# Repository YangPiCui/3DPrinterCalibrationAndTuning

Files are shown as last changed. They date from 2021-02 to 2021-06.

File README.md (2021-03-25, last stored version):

# 3DPrinterCalibrationAndTuning
Instruction is based on the Cura Slicer and Doogell Vega.  
     
a temporary value = 0.1;  //comments  
> Filament Diameter = 1.75mm; // a permanent value 

## 0. Calibrate Printer and Fix Independent Slicer Parameters
### Levelling
0. Set the hotend and the bed are at their printing temperatures. 
1. Level the print bed against the print head.
2. Level the printer with a bubble leveler on the print bed.

### 0.0 Acquire Printer Basic Parameters
X/Y uncertainty = 0.1mm;  
Z resolution = 0.04mm;    
> Max hotend temperature = 260;  
> Max bed temperature = 70;  

> X direction = ↓; X range = 0-250;  
> Y direction = →, Y range = 0-293; //Belt starts to slip at 294  
> Z direction = up, Z range = 0-175; //with glass bed. Default 300.
> Rectangular; Heated bed; G-code flavor = RepRap;  
  
Printhead ([how these values are defined](https://community.ultimaker.com/topic/18484-printhead-settings/))  
> X min = -29; //measured in the negative x direction  
> Y min = -37; //measured in the negative y direction  
> X max = 60; //measured in the positive x direction  
> Y max = 37; //measured in the positive y direction  
> Gantry Height = 82mm; //the lowest point on the rails in which the extruder assembly rides to the print bed when the nozzle is at height Z=0  
  
Extruder 0:   
> Compatible material diameter = 1.75 mm;  
> Nozzle size = 0.6mm; //default 0.4mm  
> Nozzle Flat = 1.2mm.  
    
### 0.1 Calibrate Printer XYZ Steps/mm ([reference](https://www.youtube.com/watch?v=W4CsD5lRvHY&feature=emb_logo))  
During this step, make sure the hotend is not obstructed in any direction!  

Default steps/mm X&Y = 80; Z = 400;  

X axis  
[Y = 0, Z = 3]; intended travel = 250mm; actual = 250.2mm;  
[Y = 150, Z = 3]; intended travel = 250mm; actual = 250.4mm; <- Scale Model by .99840  
[Y = 300, Z = 3]; intended travel = 250mm; actual = 250.4mm;  
  
Y axis  
[X = 0, Z = 3]; intended travel = 300mm; actual = 297.5mm;  
[X = 125, Z = 3]; intended travel = 300mm; actual = 299mm; <- Scale Model by 1.00334  
[X = 250, Z = 3]; intended travel = 300mm; actual = 298mm;  
  
Z axis  
[X = 0, Y = 0]; intended travel = 297mm; actual = 296.2mm;  
[X = 0, Y = 300]; intended travel = 297mm; actual = 296.5mm ;  
[X = 125, Y = 150]; intended travel = 297mm; actual = 297mm; <- Average of all measurements  
[X = 250, Y = 0]; intended travel = 297mm; actual = 296.2mm;  
[X = 250, Y = 300]; intended travel = 297mm; actual = 296.25mm;  

existing value * desired value / actual value = corrected value  
> X = 80 * .99840 = 79.872;  
> Y = 80 * 1.00334 = 80.267;  
> Z = 400 * 1.0019 = 400.76;  
  
### 0.2 Calibrate Printer Extruder Steps/mm (E) ([reference](https://mattshub.com/blog/2017/04/19/extruder-calibration))  
Remove the hot end.  
Calibrate when filament changes.  
Default steps/mm E = 95.8 (extrusion multiplier);  
corrected value = existing value * desired value / actual value
> E steps/mm = 96.67 * 200 / 200.5 = 96.5;  

### 0.3 Calculate Printer Max Mechanical Speed
> X/Y Max Speed = 300mm/s;  
> Z Max Speed =  12.5mm/s;   
> E Max Speed = 28 mm/s;   

### 0.4 Fix Independent Slicer Parameters 
Load default cura profile "Fine", which has a layer height of 0.1mm.  
Choose these constant parameter(s) for production print:  
> Layer height = 0.4; //A multiple of 0.04mm and should be less than 80% of nozzle diameter. [stepper motor magic number](https://www.youtube.com/watch?v=WIkT8asT90A).  [Which layer height gives you the strongest 3D prints](https://www.youtube.com/watch?v=fbSQvJJjw2Q&t=644s).  
> Line Width = 1.0; //Minimum Line Width = Nozzle Size + Layer Height;  Maximum Line Width = Nozzle Flat Size + Layer Height;  [understand line width](https://dyzedesign.com/2018/07/3d-print-speed-calculation-find-optimal-speed/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,bigger%20nozzles%20and%20layer%20height.)
> Print Speed = 50mm/s; // [Maximum 3D Printing Speed Calculator](https://dyzedesign.com/3d-printing-speed-calculator/).
> Travel Speed = 300;  
> Top/Bottom Pattern = Bottom Pattern Initial Layer = Zig Zag;  
> Infill Pattern = Gyroid;  //[increased strength for the lowest weight.](https://support.ultimaker.com/hc/en-us/articles/360012607079-Infill-settings) [Testing 3D printed infill pattern.](https://www.youtube.com/watch?v=upELI0HmzHc)
> Optimize Wall Printing Order = True;  
> Print Thin Walls = True;  
> Z Seam Alignment = Random;  

## 1. Fix Inter-dependent Slicer Parameters
### 1.0 Remove Jerk ([reference](https://all3dp.com/2/3d-printing-speed-optimal-settings/) | [reference](https://www.thingiverse.com/thing:1586548) | [Printing at 300mm/s](https://dyzedesign.com/2016/10/printing-300-mm-s-part-1-basics-hardware/) | [Motion Profile](https://www.controleng.ca/servosoft/SSHelp1033/source/MotionProfile.htm) | [reference](https://www.reddit.com/r/3Dprinting/comments/99rhah/what_is_jerk_really_measuring/))
> Print Accelaration = 250 mm/s^2;  
> Print Jerk = 0.001 mm/s; //print head's max speed at which it can change direction 

### 1.1 Optimize Cooling
> Enable Print Cooling = false; //I prefer natural cooling for better layer bonding  

### 1.2 Tune Hotend PID ([reference](https://reprap.org/wiki/PID_Tuning)) 
> The default PIDs are usually good: P = 10; I = 2.5; D = 100;  

### 1.3 Optimize Hotend Temperature [Print Some Test Objects At This Step] ([reference](https://e3d-online.dozuki.com/Guide/Calibrating+Printing+temperature/91))(https://matterhackers.dozuki.com/Guide/PID+Tuning/6)) | [reference](https://reprap.org/wiki/PID_Tuning) | [reference]([https://reprap.org/wiki/G-code#M928:_Start_SD_logging](https://reprap.org/wiki/G-code#M928:_Start_SD_logging))) 
Stack the [Smart compact temperature calibration Towers](https://www.thingiverse.com/thing:2729076)   on top of each other [in Cura](CalibrationObjects/TemperatureTower.3mf). Make sure you import the models only (without importing profiles)! Use "Extensions" -> "Post Processing" -> "ChangeAtZ" to set the temperatures.  (1.4mm, 11.4mm, 21.4mm ...)  
Infill = 15%;  
Support = No;  
Build Plate Adhesion = Skirt;  
> Printing Temperature = 210 Celsius;  
> Build Plate Temperature = 35;  //[reference](https://all3dp.com/2/the-best-pla-print-temperature-how-to-achieve-it/)  | [Correct elephant foot and print edge bending.]  

### 1.4 Minimize Stringing [Print Some Test Objects At This Step] ([reference](https://all3dp.com/2/3d-print-stringing-easy-ways-to-prevent-it/) | [reference](https://www.thingiverse.com/thing:2219103))
[StringTest.stl](CalibrationObjects/StringTest.stl)   
Wall Line Count = 3;   
Top Layers = Bottom Layers = 4;   
Infill Density = 15;  
Support = No;  
Build Plate Adhesion = skirt;  
> Retract Before Outer Wall = True;  
> Retraction Distance = 2mm;  
> Retraction Speed = 30mm/s; // same as the E Max Speed
> Combing Mode = Not in Skin;  
> Max Comb Distance With No Retract = 15mm;  
> Z Hop When Retracted = False;  
  
### 1.5 Calibrate Flow Rate [Print Some Test Objects At This Step]  ([reference](https://e3d-online.dozuki.com/Guide/Flow+rate+%28Extrusion+multiplier%29+calibration+guide./89))  
[FlowRateCalibration.3mf](CalibrationObjects/FlowRateCalibration.3mf) Make sure you import the models only (without importing profiles)!  
Wall Line Count = 2; 
Top Layers = Bottom Layers = 0;  
Infill Density = 0;  
Build Plate Adhesion Type = Brim;   
  
Corrected Flow Rate = Existing flow rate * Desired wall thickness / actual wall thickness
> Flow = 92;
(https://all3dp.com/1/common-3d-printing-problems-troubleshooting-3d-printer-issues/)  

### 1.6 Calibrate Horizontal Expansion [Print Some Test Objects At This Step] ([reference](https://www.youtube.com/watch?v=UUelLZvDelU) | [reference](https://bradshacks.com/3d-printing-tolerancing/))
[HorizontalExpansionCalibration.3mf](CalibrationObjects/HorizontalExpansionCalibration.3mf) Use "import model" instead of "import project"! 
> Connect Infill Lines;  
> Randomize Infill Start;  
Support = None;  
Build Plate Adhesion = Skirt;  
Skirt Line Count = 2;  
Skirt Distance = 5mm;  
Skirt Minimum Length = 50mm;  
> Horizontal Expansion = Initial Layer Horizontal Expansion = -0.05; //use a vernier caliber
> Hole Horizontal Expansion = 0.1; //positive value makes bigger holes

### 1.7 Optimize Initial Layer Adhesion
> Initial Layer Height = 0.4-0.1 = 0.3; // Set the initial layer height (ILH) to be the layer height (0.4mm) from the buildplate. I used a piece of paper 0.1mm thick to level the bed. ILH == multiple of Z-resolution(0.04mm) && (>= Layer Height) && (<= 80% of nozzle size) 
> Z Offset = -0.0mm; //[cura z offset simply explained](https://all3dp.com/2/cura-z-offset-simply-explained/) 
> Initial Layer Speed = 20mm/s; //[Tune First Layer.](https://www.youtube.com/watch?v=pAFDEn3wGYo)  
> Initial Layer Flow = 92*0.4/0.3 = 123; //scaled from the Flow value; = actual initial layer height / initial layer height

### 1.8 Determine Max Overhang Angle [Print Some Test Objects At This Step]
[How to calculate maximum overhang angle](https://omni3d.com/blog/how-to-calculate-maximum-overhang-angle/)   
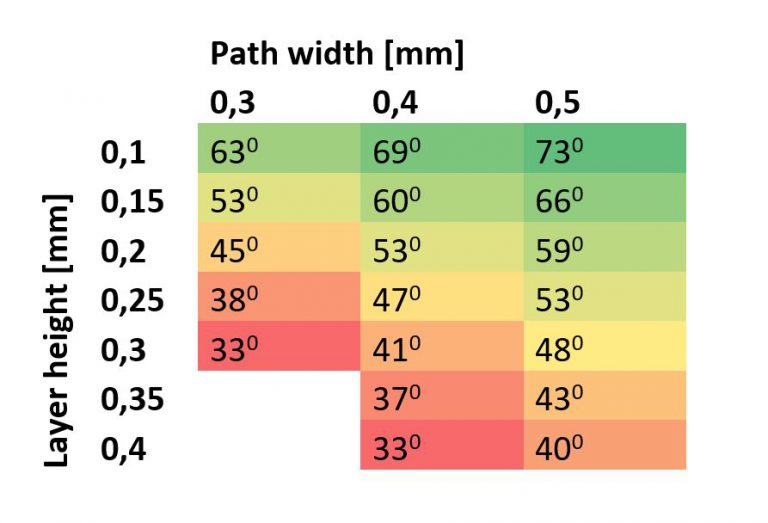
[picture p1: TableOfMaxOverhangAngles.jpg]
  
Print an overhang angle test object to confirm this.  

## 2. Miscellaneous Settings  
> Infill Travel Optimization = On;  
> Avoid Supports When Travelling = True;  
> Slicing Tolerance = Inclusive;  
   
### 2.0 Situational Settings  
> Wall Line Count = Top Layers = Bottom Layers = 6; //[3-4 layers && 15-20% for good strength. Max strength with 5-6 layers and 25-30% infill.](https://www.youtube.com/watch?v=sAZpnlzCwiU)  
> Infill = 30%;  
> Infill Pattern = Gyroid;
> Top/Bottom Pattern = Zig Zag;
> Bottom Pattern Initial Layer = Zig Zag; // Top Bottom Layer number a multiple of 2 preferred
> Build Plate Adhesion Type = Brim;  
> Brim Line Count = 1;
> Tree Support Branch Angle = 30; // This depends on the layer height and line width of the tree support walls
> Use Adaptive Layers = True; //set to false by default.
> Adaptive Layers Maximum Variation = 0.08; //half of line height  
> Adaptive Layers Variation Setp Size = 0.04;  
> Adaptive Layers Topography Size = 0.16; //same as line height

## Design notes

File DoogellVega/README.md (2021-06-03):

# Doogell Vega
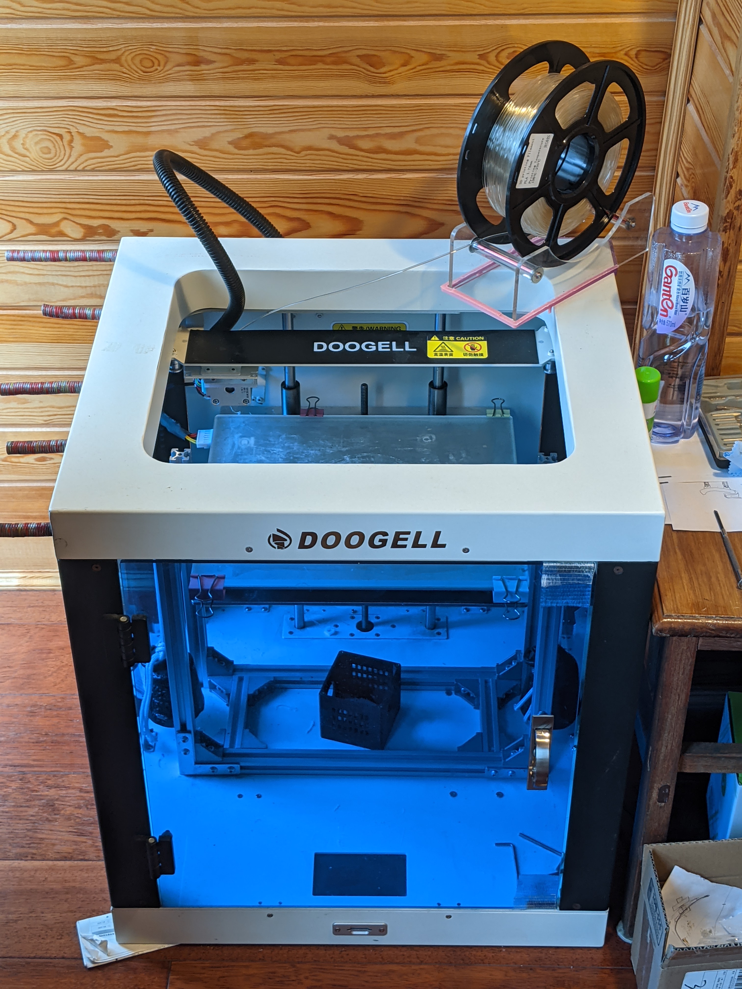
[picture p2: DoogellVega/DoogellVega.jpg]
  
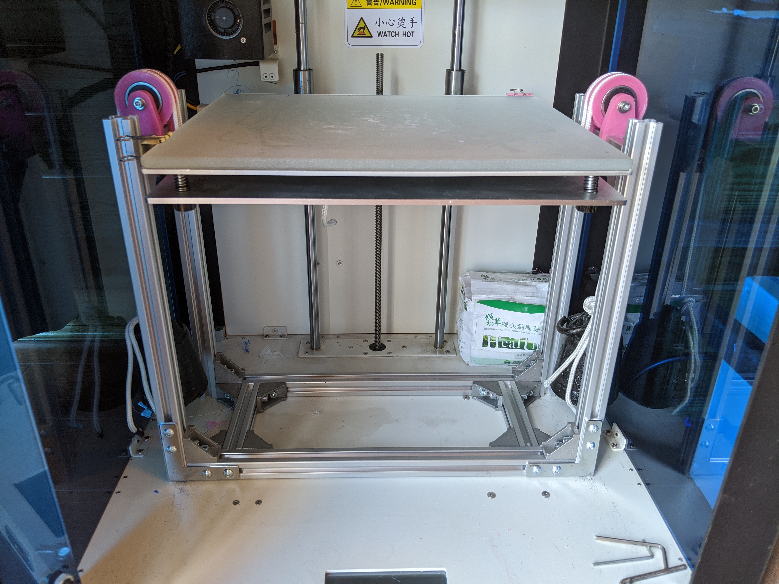
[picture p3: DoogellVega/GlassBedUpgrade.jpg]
  
Bought 2nd hand for $500; CoreXY structure; Imported stepper motors and linear rails.  
Touch screen is inaccurate to the touch; One has to use Gcode to change the default printer parameters.   
Rectangular build plate; Heated bed; Replaced bed cover with tempered sanded-surface glass.   
Added plexiglass hud.
     
Instruction is based on the Cura Slicer.  
a temporary value = 0.1;  //comments  
> Filament Diameter = 1.75mm; // a permanent value 

## 0. Calibrate Printer and Set Independent Slicer Parameters
### 0.0 Bed Levelling
0. Set the hotend and the bed at their intended printing temperatures. 
1. Level the print bed against the print head with a strip of A4 paper (usually 0.1mm thick).
2. Level the entire printer with a bubble leveler placed on the print bed.

### 0.1 Acquire Printer Specifications
> Filament Diameter = 1.75mm;  
> Rectangular; Heated bed; G-code flavor = RepRap;  
> Max hotend temperature = 260;  
> Max bed temperature = 70;  
> X direction = ↓; X range = 0-250; //Positive direction from the back to the front  
> Y direction = →, Y range = 0-240; //Belt starts to slip at 294; fan mod limits travel to 240
> Z direction = up, Z range = 0-200; //for glass bed; Default is 300.   
> X/Y resolution = 0.1mm;  
> Z resolution = 0.04mm;  
  
Printhead ([how these values are defined](https://community.ultimaker.com/topic/18484-printhead-settings/))  
> X min = -29-9; //measured in the negative x direction  
> Y min = -37-12; //measured in the negative y direction  
> X max = 60; //measured in the positive x direction  
> Y max = 37+13; //measured in the positive y direction  
> Gantry Height = 92+13mm; //the lowest point on the rails in which the extruder assembly rides to the print bed when the nozzle is at height Z=0   
  
Extruder 0:    
> Nozzle size = 0.3mm; //default 0.4mm
> Nozzle Flat = 1.2mm.  
    
### 0.2 Calibrate Printer XYZ Steps/mm ([reference](https://www.youtube.com/watch?v=W4CsD5lRvHY&feature=emb_logo))  
During this step, make sure the hotend is not obstructed in any direction!  

Default steps/mm X&Y = 80; Z = 400;  //(Machine LCD screen under "Advanced Settings")   

X axis  
[Y = 0, Z = 3]; intended travel = 250mm; actual = 250.2mm;  
[Y = 150, Z = 3]; intended travel = 250mm; actual = 250.4mm; <- Scale Model by .99840  
[Y = 300, Z = 3]; intended travel = 250mm; actual = 250.4mm;  
  
Y axis  
[X = 0, Z = 3]; intended travel = 300mm; actual = 297.5mm;  
[X = 125, Z = 3]; intended travel = 300mm; actual = 299mm; <- Scale Model by 1.00334  
[X = 250, Z = 3]; intended travel = 300mm; actual = 298mm;  
  
Z axis  
[X = 0, Y = 0]; intended travel = 297mm; actual = 296.2mm;  
[X = 0, Y = 300]; intended travel = 297mm; actual = 296.5mm ;  
[X = 125, Y = 150]; intended travel = 297mm; actual = 297mm; <- Average of all measurements  
[X = 250, Y = 0]; intended travel = 297mm; actual = 296.2mm;  
[X = 250, Y = 300]; intended travel = 297mm; actual = 296.25mm;  

existing value * desired value / actual value = corrected value  
> X = 80 * .99840 = 79.872;  
> Y = 80 * 1.00334 = 80.267;  
> Z = 400 * 1.0019 = 400.76;  
  
Apply the Gcodes in "SetXYZStepsPerMm.gcode" to save the calibrated values.  
  
### 0.3 Calibrate Printer Extruder Steps/mm (E) ([reference](https://mattshub.com/blog/2017/04/19/extruder-calibration))  
Remove the hot end.  
Calibrate when filament changes.  
Default steps/mm E = 95.8 (extrusion multiplier);  
corrected value = existing value * desired value / actual value
> E steps/mm = 96.67 * 200 / 200.5 = 96.5;  

### 0.4 Calculate Printer Max Mechanical Speed
Apply the Gcodes in "MeasureXYZMaxSpeeds.gcode" to measure the max speeds.  
> X/Y Max Speed = 300mm/s; //approximation  
> Z Max Speed =  12.5mm/s; //approximation  
> E Max Speed = 28 mm/s; //filament extrusion speed     

### 0.5 Tune PID
> Default PID works well: P = 10; I = 2.5; D = 100; (Machine LCD screen under "Advanced Settings")  
  
The printer can not display the results of PID auto tuning on its LCD screen; Neither can it log the results onto a SD card.  
Integrate TuneAndLogTemperaturePID.gcode into the printer's Start G-code in Cura to set and to save the temperature PID. 
  
### 0.6 Set Independent Slicer Parameters 
Load default cura profile "Fine", which has a layer height of 0.1mm.  
Choose these constant parameter(s) for production print:  
> Layer height = 0.4; //A multiple of 0.04mm and should be less than 80% of nozzle diameter. [stepper motor magic number](https://www.youtube.com/watch?v=WIkT8asT90A).  [Which layer height gives you the strongest 3D prints](https://www.youtube.com/watch?v=fbSQvJJjw2Q&t=644s).  
> Line Width = 1.0; //Minimum Line Width = Nozzle Size + Layer Height;  Maximum Line Width = Nozzle Flat Size + Layer Height;  [understand line width](https://dyzedesign.com/2018/07/3d-print-speed-calculation-find-optimal-speed/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,bigger%20nozzles%20and%20layer%20height.)
> Print Speed = 50mm/s; // [Maximum 3D Printing Speed Calculator](https://dyzedesign.com/3d-printing-speed-calculator/).
> Travel Speed = 300;  
> Top/Bottom Pattern = Bottom Pattern Initial Layer = Zig Zag;  
> Infill Pattern = Gyroid;  //[increased strength for the lowest weight.](https://support.ultimaker.com/hc/en-us/articles/360012607079-Infill-settings) [Testing 3D printed infill pattern.](https://www.youtube.com/watch?v=upELI0HmzHc)
> Optimize Wall Printing Order = True;  
> Print Thin Walls = True;  
> Z Seam Alignment = Random;  

## 1. Fix Inter-dependent Slicer Parameters
### 1.0 Remove Jerk ([reference](https://all3dp.com/2/3d-printing-speed-optimal-settings/) | [reference](https://www.thingiverse.com/thing:1586548) | [Printing at 300mm/s](https://dyzedesign.com/2016/10/printing-300-mm-s-part-1-basics-hardware/) | [Motion Profile](https://www.controleng.ca/servosoft/SSHelp1033/source/MotionProfile.htm) | [reference](https://www.reddit.com/r/3Dprinting/comments/99rhah/what_is_jerk_really_measuring/))
> Print Accelaration = 250 mm/s^2;  
> Print Jerk = 0.001 mm/s; //print head's max speed at which it can change direction
Cura generated jerk G-code is 0.06 mm/s for some reason.    
The Cura settings alone doesn't affect printer acceleration. Put these values in the Start G-code using the commands M201, M202, and M566. See "StartAndEndG-code.txt" for the tuned values. 

### 1.1 Optimize Cooling
> Enable Print Cooling = false; //I prefer natural cooling for better layer bonding  
  
Minimum layer time = 20;
Minimum Speed = 0.25;

### 1.2 Tune Hotend PID ([reference](https://reprap.org/wiki/PID_Tuning)) 
> The default PIDs are usually good: P = 10; I = 2.5; D = 100;  

### 1.3 Optimize Hotend Temperature [Print Some Test Objects At This Step] ([reference](https://e3d-online.dozuki.com/Guide/Calibrating+Printing+temperature/91))(https://matterhackers.dozuki.com/Guide/PID+Tuning/6)) | [reference](https://reprap.org/wiki/PID_Tuning) | [reference]([https://reprap.org/wiki/G-code#M928:_Start_SD_logging](https://reprap.org/wiki/G-code#M928:_Start_SD_logging))) 
Stack the [Smart compact temperature calibration Towers](https://www.thingiverse.com/thing:2729076)   on top of each other [in Cura](CalibrationObjects/TemperatureTower.3mf). Make sure you import the models only (without importing profiles)! Use "Extensions" -> "Post Processing" -> "ChangeAtZ" to set the temperatures.  (1.4mm, 11.4mm, 21.4mm ...)  
Infill = 15%;  
Support = No;  
Build Plate Adhesion = Skirt;  
> Printing Temperature = 210 Celsius;  
> Build Plate Temperature = 35;  //[reference](https://all3dp.com/2/the-best-pla-print-temperature-how-to-achieve-it/)  | [Correct elephant foot and print edge bending.]  

### Improve Surface Quality (Blobs, Zigs, Stringing and Oozing) [Print Some Test Objects At This Step] ([reference](https://all3dp.com/2/3d-print-stringing-easy-ways-to-prevent-it/) | [reference](https://www.thingiverse.com/thing:2219103))
[StringTest.stl](CalibrationObjects/StringTest.stl)   
Wall Line Count = 3;   
Top Layers = Bottom Layers = 4;   
Infill Density = 15;  
Support = No;  
Build Plate Adhesion = skirt;  
> Retract Before Outer Wall = True;  
> Retraction Distance = .8mm;  
> Retraction Speed = 30mm/s; // same as the E Max Speed
> Combing Mode = Not in Skin;  
> Max Comb Distance With No Retract = 15mm;  
> Travel Avoid Distance = 1/1; // Greater than half of nozzle flat diameter and multiple of XY resolution
> Z Hop When Retracted = False;  
> Travel Avoid Distance = 1mm; // take nozzle flat into account

> Coasting Volume
> Coasting Speed

> Retraction Extra Prime Amount
  
### 1.5 Calibrate Flow Rate [Print Some Test Objects At This Step]  ([reference](https://e3d-online.dozuki.com/Guide/Flow+rate+%28Extrusion+multiplier%29+calibration+guide./89))  
[FlowRateCalibration.3mf](CalibrationObjects/FlowRateCalibration.3mf) Make sure you import the models only (without importing profiles)!  
Wall Line Count = 2; 
Top Layers = Bottom Layers = 0;  
Infill Density = 0;  
Build Plate Adhesion Type = Brim;   
  
Corrected Flow Rate = Existing flow rate * Desired wall thickness / actual wall thickness
> Flow = 92;
(https://all3dp.com/1/common-3d-printing-problems-troubleshooting-3d-printer-issues/)  

### 1.6 Calibrate Horizontal Expansion [Print Some Test Objects At This Step] ([reference](https://www.youtube.com/watch?v=UUelLZvDelU) | [reference](https://bradshacks.com/3d-printing-tolerancing/))
[HorizontalExpansionCalibration.3mf](CalibrationObjects/HorizontalExpansionCalibration.3mf) Use "import model" instead of "import project"! 
> Connect Infill Lines;  
> Randomize Infill Start;  
Support = None;  
Build Plate Adhesion = Skirt;  
Skirt Line Count = 2;  
Skirt Distance = 5mm;  
Skirt Minimum Length = 50mm;  
> Horizontal Expansion = Initial Layer Horizontal Expansion = -0.05; //use a vernier caliber
> Hole Horizontal Expansion = 0.1; //positive value makes bigger holes

### 1.7 Optimize Initial Layer Adhesion
> Initial Layer Height = 0.4-0.1 = 0.3; // Set the initial layer height (ILH) to be the layer height (0.4mm) from the buildplate. I used a piece of paper 0.1mm thick to level the bed. ILH == multiple of Z-resolution(0.04mm) && (>= Layer Height) && (<= 80% of nozzle size) 
> Z Offset = -0.0mm; //[cura z offset simply explained](https://all3dp.com/2/cura-z-offset-simply-explained/) 
> Initial Layer Speed = 20mm/s; //[Tune First Layer.](https://www.youtube.com/watch?v=pAFDEn3wGYo)  
> Initial Layer Flow = 92*0.4/0.3 = 123; //scaled from the Flow value; = actual initial layer height / initial layer height

### 1.8 Determine Max Overhang Angle [Print Some Test Objects At This Step]
[How to calculate maximum overhang angle](https://omni3d.com/blog/how-to-calculate-maximum-overhang-angle/)   
  
Print an overhang angle test object to confirm this.  

## 2. Miscellaneous Settings  
> Infill Travel Optimization = On;  
> Avoid Supports When Travelling = True;  
> Slicing Tolerance = Inclusive;  
   
### 2.0 Situational Settings  
> Wall Line Count = Top Layers = Bottom Layers = 6; //[3-4 layers && 15-20% for good strength. Max strength with 5-6 layers and 25-30% infill.](https://www.youtube.com/watch?v=sAZpnlzCwiU)  
> Infill = 30%;  
> Infill Pattern = Gyroid;
> Top/Bottom Pattern = Zig Zag;
> Bottom Pattern Initial Layer = Zig Zag; // Top Bottom Layer number a multiple of 2 preferred
> Build Plate Adhesion Type = Brim;  
> Brim Line Count = 1;
> Tree Support Branch Angle = 30; // This depends on the layer height and line width of the tree support walls
> Use Adaptive Layers = True; //set to false by default.
> Adaptive Layers Maximum Variation = 0.08; //half of line height  
> Adaptive Layers Variation Setp Size = 0.04;  
> Adaptive Layers Topography Size = 0.16; //same as layer height

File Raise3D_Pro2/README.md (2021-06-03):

# [Raise3D Pro2](https://www.raise3d.com/products/pro2-3d-printer/) 
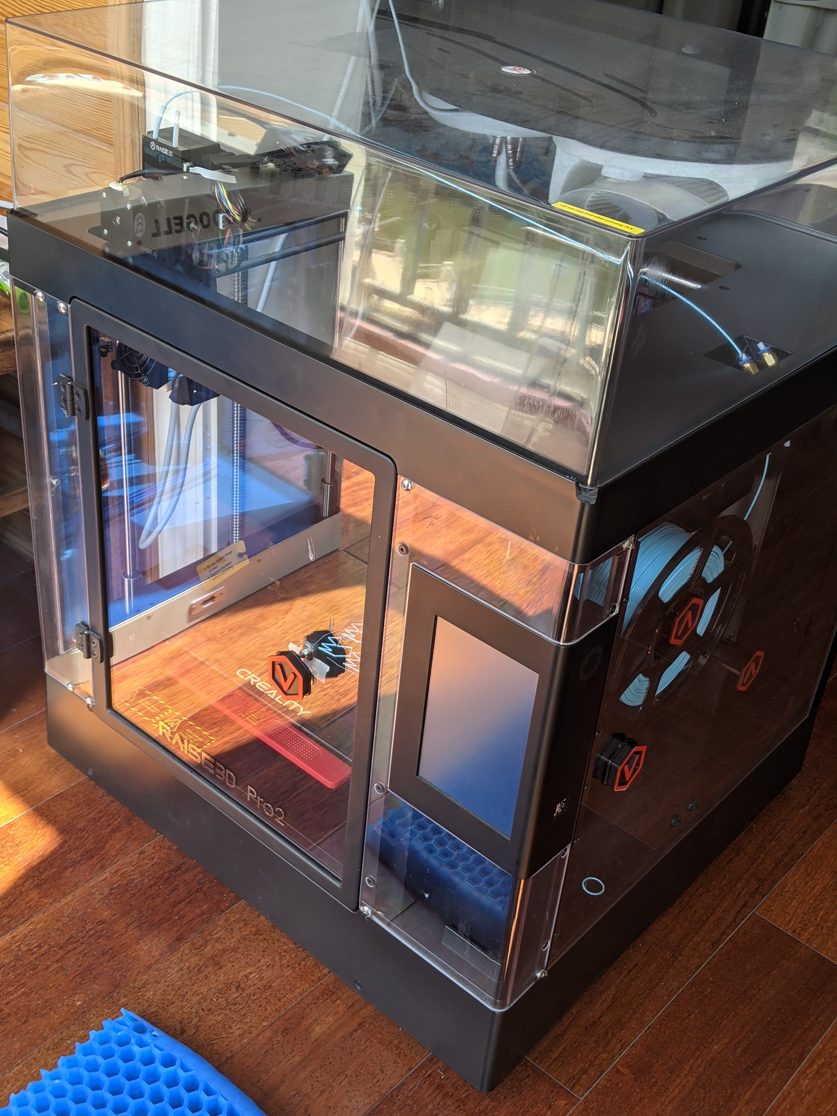
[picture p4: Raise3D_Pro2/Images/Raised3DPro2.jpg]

Bought 2nd hand for $2600.  
This printer lacks water cooling and needs the linear advance feature.  
Coasting cannot compensate for linear advance because one, there is no feature to compensate for the material lost during coasting; two, the amount of coasted material depends on the print speed.  
[Questioning Pro2 Product Quality - Ongoing Issues](https://forum.raise3d.com/viewtopic.php?f=18&t=15999&sid=b55814a84943acde992d9dc563f45d35)  
Instruction is based on the Cura Slicer which has the Tree Support Structure.  
a temporary value = 0.1;  //comments  
> Filament Diameter = 1.75mm; // a permanent setting   

## 0. Calibrate Printer

### Acquire Printer Specifications
> Rectangular; Heated bed; G-code flavor = Marlin;  
> Max hotend temperature = 310 Celsius;  
> Max bed temperature = 110;  
> X direction = →; X range = 0-295; // The gantry hits the belt beyond this point
> Y direction = ↑, Y range = 0-295; // The belt grinds beyond this point
> Z direction = up, Z range = 0-295; // The bed hits the metal bottom beyond this point.
> X/Y resolution = 0.0078125mm; // Remember to put a multiple of this as the silcer resolution.
> Z resolution = 0.00078125mm; // A layer height of 0.3mm is an integer multiple of the Z resolution.
  
Printhead Dimension wrt 0th Nozzle ([how these values are defined](https://community.ultimaker.com/topic/18484-printhead-settings/))  
> X min = -37+3; //measured in the negative x direction  
> Y min = -45-12; //measured in the negative y direction  
> X max = 63; //measured in the positive x direction  
> Y max = 70; //measured in the positive y direction  
> Gantry Height = 65+5mm; //the lowest point on the rails in which the extruder assembly rides to the print bed when the nozzle is at height Z=0   
  
Extruder 0:    
> Nozzle size = 0.4mm; // I used carbon hardened aftermarket steel nozzles. This saves me effort from changing nozzles.
> Nozzle Flat = 1.6mm;
  
Extruder 1:    
> Nozzle size = 0.3mm; 
> Nozzle Flat = 1.6mm;
> Nozzle Offset X = 25.3; //This is relative to the 0th nozzle. This value needs to be tuned. 
> Nozzle Offset Y = -0.2mm;
> Cooling Fan Number = 1;  
    
### Calibrate Printer XYZ Steps/mm ([reference](https://www.youtube.com/watch?v=W4CsD5lRvHY&feature=emb_logo))  
During this step, make sure the hotend is not obstructed in any direction!  
corrected value = existing value * desired value / actual value  
Default steps/mm X&Y = 80; Z = 800; //default settings are spot on  
  
### Calibrate Printer Extruder Steps/mm (The extrusion multiplier E) ([reference](https://mattshub.com/blog/2017/04/19/extruder-calibration))  
Remove the hot end. Calibrate when filament changes.  
Default steps/mm E = 6640;  //(default setting should be also spot on)[https://forum.raise3d.com/viewtopic.php?f=18&t=20580&hilit=extrusion+rate]

### Measure Printer Max Mechanical Speed
Use MeasureXYZMaxSpeeds.gcode and a stop-watch.  
> X/Y Max Speed = 50mm/s; //Measured
> Z Max Speed =  5mm/s; //Measured  
> E Max Speed = 40mm/s; //From IdeaMaker; assumed.  

### Level Print Bed
0. Set the hotend and the bed at their intended printing temperatures. Hotend 210C; Buildplate 45C.  
1. Remove the removable parts of the bed assembly. Level the print bed against the print head with a digital indicator. See [Bed Leveling/Tramming a Raise3D N2 or N2 Plus](https://www.youtube.com/watch?v=MXAk4eBr21g&ab_channel=ViceChief) I 3D-printed an adaptor to mount the digital indicator to the hot end clamps. See the CustomUpgrades folder.
2. Level the entire printer with a bubble leveler placed on the print bed.  

### Tune Hotend and Printbed PIDs ([reference](https://reprap.org/wiki/PID_Tuning))  
Apply printer's PID auto tune feature.

### StartEndG-codes.txt
[Cura G-code has some perks](https://github.com/Ultimaker/Cura/issues/6383).  
Don't use the below G-code. Once set, it would always use the 1th of the 0th extruder as the initial extruder.  
Print long skirt/brim lines to prime the nozzle head for single extrusion mode instead.  
> T1  ;or T0
> G1 F200 E{switch_extruder_retraction_amount}      ;Extrude filament  
  
References:  
* [Cura keywords](https://github.com/Ultimaker/Cura/blob/master/resources/definitions/fdmprinter.def.json)
* IdeaMaker Settings and output G-codes
* [Github](https://github.com/Raise3D/Marlin-Raise3D-N-Series/blob/master/Marlin/Marlin_main.cpp)
* [Forum](https://forum.raise3d.com/viewtopic.php?t=16362)
  
## 1. Set Initial Slicer Parameters
Load default cura profile "Extra Fast", which has a layer height of 0.3mm.  
Oozing is the bane of dual extrusion. I decided to deploy Pro2 as a single extruder system. For this to work, treat it as a dual extruder in Cura but only enable one of the extruders.  
  
> Layer height = 0.3/0.15; //An integer multiple of the Z resolution and should be less than 80% of nozzle diameter. [stepper motor magic number](https://www.youtube.com/watch?v=WIkT8asT90A).  [Which layer height gives you the strongest 3D prints](https://www.youtube.com/watch?v=fbSQvJJjw2Q&t=644s).  
> Initial Layer Height = 0.3-0.1 = 0.2/0.05; // Set the initial layer height (ILH) so that the distance from the buildplate is the layer height. I used a piece of paper 0.1mm thick to level the bed. ILH == multiple of Z-resolution && (<= 80% of nozzle size) 
> Line Width = 0.7/0.45; //Minimum Line Width = Nozzle Size + Layer Height;  Maximum Line Width = Nozzle Flat Size + Layer Height;  [understand line width](https://dyzedesign.com/2018/07/3d-print-speed-calculation-find-optimal-speed/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,bigger%20nozzles%20and%20layer%20height.)
> Support Line Width = 0.3/0.3; //Experiment with a smaller than nozzle diameter support line width. If the right extruder is selected as the support extruder, Cure automatically uses its line width as the support line width.
   
> Wall Line Count = Top Layers = Bottom Layers = 4; //[1-2-3-4-5-6 layers <=> 5-10-15-20-25-30% Infill](https://www.youtube.com/watch?v=sAZpnlzCwiU) 
> Infill = 20%;  
> Top/Bottom Pattern = Bottom Pattern Initial Layer = Zig Zag;  //Prefer Top Bottom Layer number a multiple of 2 if Zig Zag
> Optimize Wall Printing Order = True;  
> Print Thin Walls = True;  
> Infill Pattern = Gyroid;  //[increased strength for the lowest weight.](https://support.ultimaker.com/hc/en-us/articles/360012607079-Infill-settings) [Testing 3D printed infill pattern.](https://www.youtube.com/watch?v=upELI0HmzHc)
> Connect Infill Lines;  
> Randomize Infill Start;  
> Infill Travel Optimization = On;  

### Tune Print Speed (extrusion rate), Jerk and Acceleration
Ideally, the hotend assembly should always apply the user specified acceleration to decelerate into and accelerate from its lowest continuous mechanical speed (the speed below which motor ticking is apparent), as determined by the physical motors. As [jerk is the speed the hotend assembly slows down to on corners](https://community.ultimaker.com/topic/21306-how-to-prevent-overshoot-corners-or-round-edges/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), the jerk value should be set to the minimum continuous mechanical speed. Due to a lack of the linear advance feature to compensate for the filament pressure change however, too slow a jerk value could make the hotend stay too long at the corners overextruding there. This is apparent in the test print image below. One can clearly see that a jerk value slower than print speed leads to uneven lines.  
   
Therefore, set as high a XY jerk value as possible to minimize mechanical stress and set the print speed equal to the jerk value. Set as low a Z jerk as possible, which is also a multiple of the step size.  
Cura uses deprecated G-code for these settings. Implement tweeked jerk an acceleration value in the start G-codes with the commands M201, M204, M205 and M500. [Marlin G-codes](https://marlinfw.org/docs/gcode/M204.html)).  
> XY Jerk = Print Speed = Outer/Inner Wall Speed = Top/Bottom Speed = Support Speed = 20/20mm/s;  //Set jerk value to be a multiple of the travel resolution. Oozing determines the minimum jerk speed. Print speed should be <50% of the [Maximum 3D Printing Speed](https://dyzedesign.com/3d-printing-speed-calculator/) When the second extruder is selected as the support extruder, Cura automatically uses its print speed as the support speed. 
> Initial Layer Speed = 20mm/s; //[Tune First Layer.](https://www.youtube.com/watch?v=pAFDEn3wGYo)  
> Support Speed = 75/140; // set to <80% of the max print speed.
> Travel Speed = 150 //Max mechanical speed
  
With the jerk and print speed set, next tune the acceleration. Assume a bed gap of 0.1mm and 5mm/s bed travel speed, the minimum acceleration for the bed to not hit the nozzle can be calculated from the acceleration equation to be 50mm/s2. Pro2's default jerk of 5mm/s and XY acceleration of 500mm/s2 works well.   
 
### Set Temperatures 
> Printing Temperature = 200/195 Celsius;  // Set and use a temperature tower to tune later.
> Initial / Final Printing Temperature / Standby Temperature = 200/195; // Set this to be equal to the print temperature to save print time.
> Build Plate Temperature = 35;  //Prefer levelling the bed at this temperature. 
> Z Hop after Extruder Switch Height = 0mm/0mm;  // Z Hop cases layers to misalign.

### Optimize Part Cooling
I customized all fans to cool the hot end instead of the printed parts.  
> Minimum Layer Time = 20s;  // Time required for a droplet of filament to cool and harden naturally.
> Minimum Layer Speed = 4mm/s;  // Same as jerk, which is effectively the minimum speed. 

### Calibrate Flow Rate 
Scale the calibration cube so that minimum layer time is met. Line width can change when print speed increases.
Wall Line Count = 2; 
Top Layers = Bottom Layers = 0;  
Infill Density = 0;    
 
Corrected Flow Rate = Existing flow rate * Desired wall thickness / actual wall thickness
> Flow = 95/95;
(https://all3dp.com/1/common-3d-printing-problems-troubleshooting-3d-printer-issues/)
> Initial Layer Flow = 100%*0.3/0.2 = 150/300; // compensates for the gap between the nozzle and the bed

### Improve Bed Adhesion 
Use long skirt line instead of extruding waste material with start Gcode.  
> Build Plate Adhesion Type = Skirt; // Set to none to print brim for features such as Support and the Prime Tower only
> Build Plate Adhesion Extruder = ; // Use the secondary/support extruder to first draw the inside skirt line. This cleans waste material the best.
> Skirt/Brim Minimum Length = 0/3; // Use a value of 0 to disable left extruder brim for the Prime Tower
> Skirt Line Count = 2; 

### Calibrate Extruder Offset from each other
Print the calibration object in folder "CalibrationObjects/DualExtruderCalibration".  
Use Cura instead of Raise3D Pro2's console to apply these settings.

### Determine Max Overhang Angle and Minimize Support Structure
[How to calculate maximum overhang angle](https://omni3d.com/blog/how-to-calculate-maximum-overhang-angle/)   
  
Print an overhang angle test object to confirm this. 

> Tree Support Branch Angle = 20; // This depends on the layer height and line width of the tree support walls
> Tree Support Branch Distance = Tree Support Branch Diameter = 1.4;  //multiple of line width
> Tree Support Branch Diameter Angle = 2.5;
> Tree Support Collision Resolution = 0.125; //multiple of resolution
> Support Placement = Everywhere; // works well with a thin support wall
> Support Overhang Angle = 41;
> Support Wall Line Count = 1;
> Support Density = 0;
> Enable Support Brim = True;
> Support Brim Line Count = 1;
> Support Top Distance = Support XY Distance = 0.6;  //twice layer height
> Support Stair Step Height = 0;

### Improve Surface Quality (Seams, Blobs, Zigs, Stringing and Oozing)
[Blobs and Zigs](https://www.simplify3d.com/support/print-quality-troubleshooting/blobs-and-zits/)  
Oozing is unavoidable. Molten filament droops under gravity.  
Filament retraction does not suck the molten filament. It merely relieves downward pressure.   
Ideally, the inactive nozzle is swiped on the support to remove its ooze, periodically and/or before it touches the printed area.  
Sadly, Pro2's inactive nozzle does not automatically lower to be wiped on Cura's Prime Tower; neither can the head-lifting feature be disabled.  

[Linear Advance](https://www.youtube.com/watch?v=n3yK0lJ8TWM&ab_channel=TeachingTech) minimizes Z Seams and blobs. Unfortunately [the pro2 doesn't have this feature yet.](https://forum.raise3d.com/viewtopic.php?t=21018)  Slow prints to compensate for now.  
> Z Seam Alignment = Random;  
> Retraction Distance = 0.8/0.8;  // Proportional to nozzle diameter
> Retraction Speed = 40/40mm/s; // From IdeaMaker, same as the E Max Speed
> Combing Mode = Not in Skin; //Move in printed area so that oozed material is deposited on top thereof.
> Max Comb Distance With No Retract = 15mm;  
> Retract Before Outer Wall = True;  
> Travel Avoid Distance = 1/1; // Greater than half of nozzle flat diameter and multiple of XY resolution

### Calibrate Horizontal Expansion [Print Some Test Objects At This Step] ([reference](https://www.youtube.com/watch?v=UUelLZvDelU) | [reference](https://bradshacks.com/3d-printing-tolerancing/))
[HorizontalExpansionCalibration.3mf](CalibrationObjects/HorizontalExpansionCalibration.3mf) Use "import model" instead of "import project"! 
Support = None;  
Build Plate Adhesion = Skirt;  
Skirt Line Count = 2;  
Skirt Distance = 5mm;  
Skirt Minimum Length = 50mm;  
> Horizontal Expansion = Initial Layer Horizontal Expansion = -0.05; //Negative value makes outside of the part smaller.
> Hole Horizontal Expansion = 0.1; //positive value makes bigger holes

### Miscellaneous Settings  
> Maximum Resolution / Travel Resolution = 0.25mm; //https://www.cnckitchen.com/blog/removing-zits-and-blobs-on-your-3d-prints-adjust-your-slicing-resolution
> Maximum Deviation = 0.05;
> Minimum Polygon Circumference = 0.25mm;
> Slicing Tolerance = Inclusive;  
> Use Adaptive Layers = True; //set to false by default.
> Adaptive Layers Maximum Variation = 0.05; //half of line height and ensure less than maximum layer height 
> Adaptive Layers Variation Setp Size = 0.025;  // printer z step size
> Adaptive Layers Topography Size = 0.15; //same as layer height

### Dual Extrusion (Avoid)
> Enable Prime Tower = True; 
> Prime Tower Size = 10; //The prime tower's diameter should be larger than the nozzle separation for the inactive extruder's ooze to be cleaned onto it.
> Prime Tower Minimum Volume = 1;
> Wipe Inavtive Nozzle on Prime Tower = True; //Pro2's entire nozzle retracts, lessoning this feature's effectiveness
> Nozzle Switch Retraction Distance = 8/8mm; //Unmolten, solid filament should clear the hotend assembly.
> Nozzle Switch Retraction Speed = 40mm/s;

> Enable Ooze Shield = True;

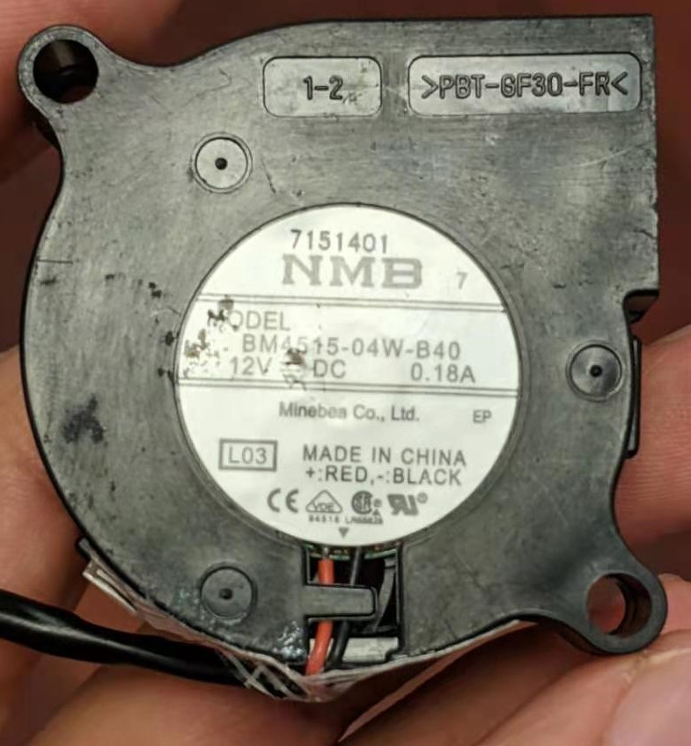
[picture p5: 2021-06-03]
Raise3D_Pro2/CustomUpgrades/BlowerFanMount/FanSpecification.JPG

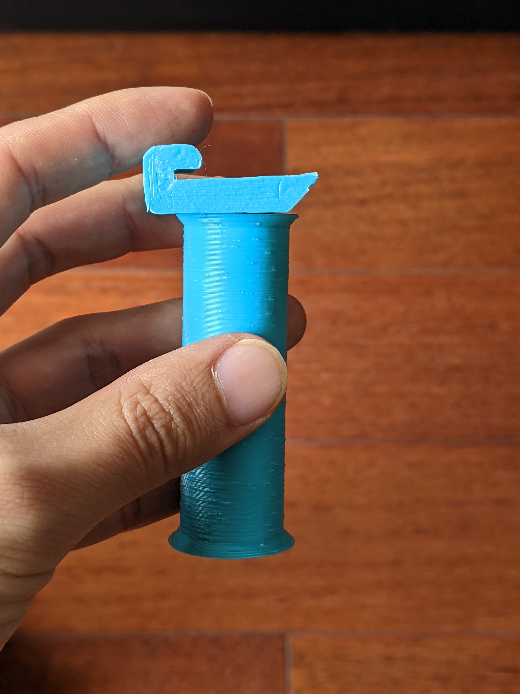
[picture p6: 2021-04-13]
Raise3D_Pro2/CustomUpgrades/FilamentSpoolMount/FilamentSpoolMount1.jpg

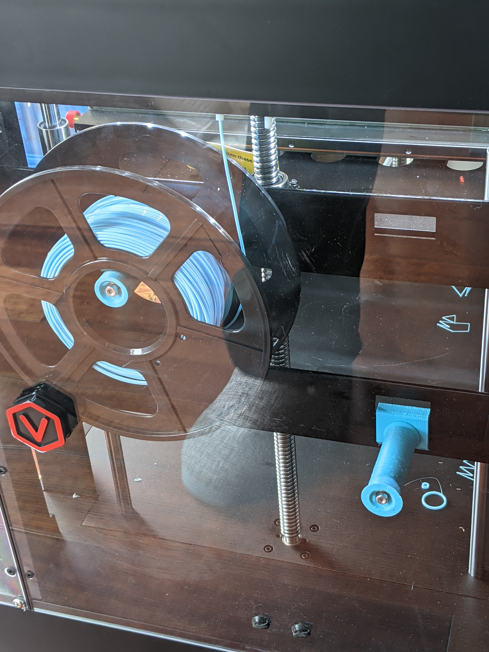
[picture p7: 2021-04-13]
Raise3D_Pro2/CustomUpgrades/FilamentSpoolMount/FilamentSpoolMount0.jpg

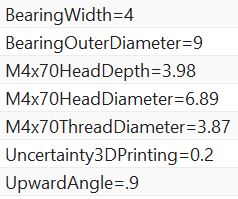
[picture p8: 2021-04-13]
Raise3D_Pro2/CustomUpgrades/FilamentSpoolMount/FilamentSpoolMount3.jpg

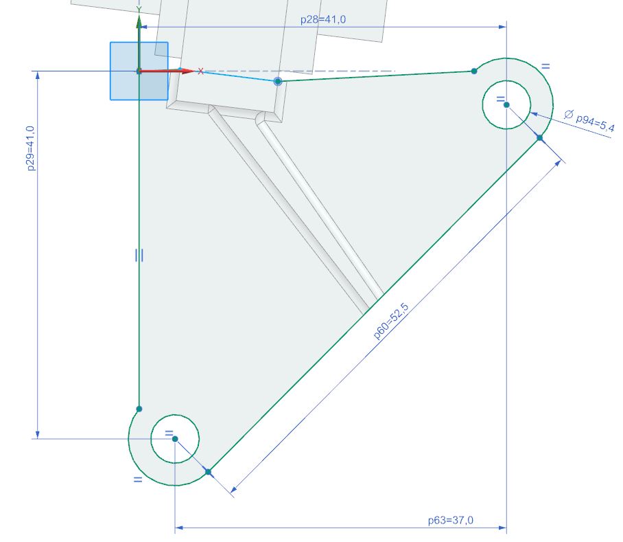
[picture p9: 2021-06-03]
Raise3D_Pro2/CustomUpgrades/BlowerFanMount/FanDimensions.JPG

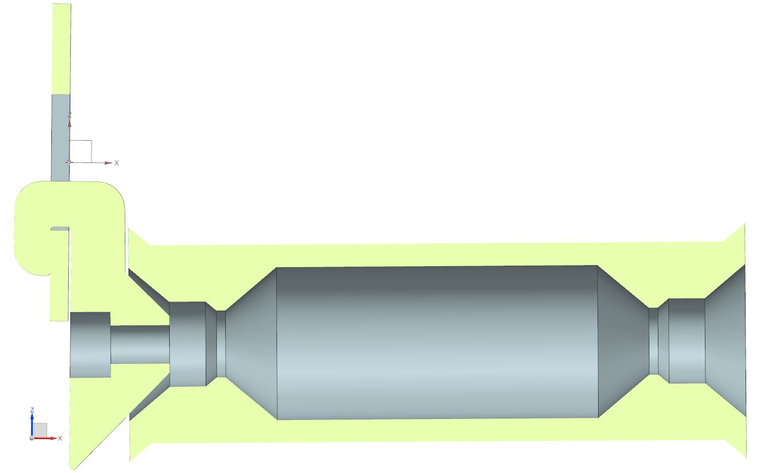
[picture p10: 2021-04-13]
Raise3D_Pro2/CustomUpgrades/FilamentSpoolMount/FilamentSpoolMount2.jpg

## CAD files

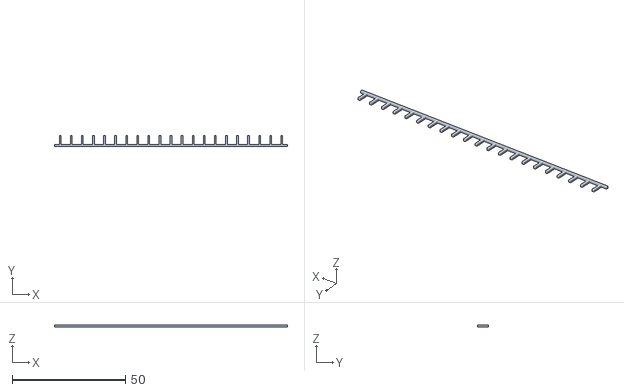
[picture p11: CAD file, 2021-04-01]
CalibrationObjects/DualExtruderCalibration/dual_calibration_v2_b.stl
103.0 x 4.80 x 0.8

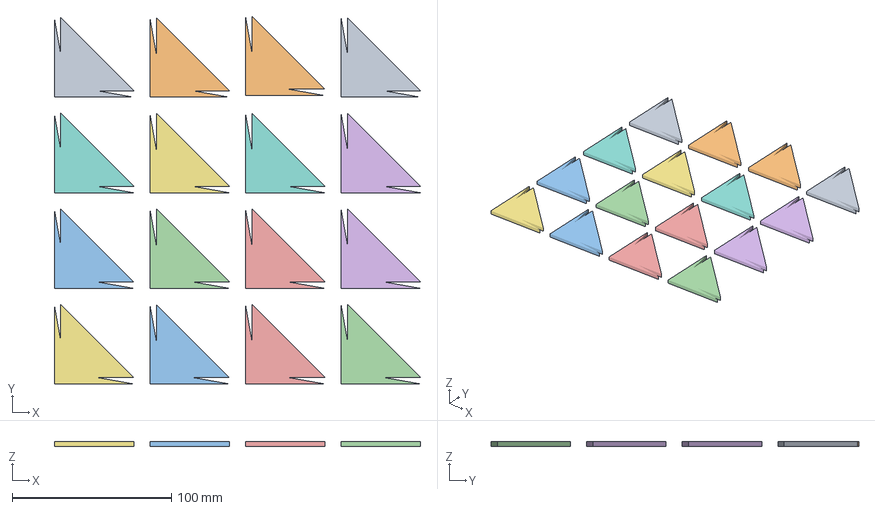
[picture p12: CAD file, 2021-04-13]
CalibrationObjects/JerkAcceleration.3mf
230.0 x 231.0 x 3.00 mm
JerkAcceleration.3mf
JerkAcceleration.3mf(1)
JerkAcceleration.3mf(2)
JerkAcceleration.3mf(3)
JerkAcceleration.3mf(4)
JerkAcceleration.3mf(5)
JerkAcceleration.3mf(6)
JerkAcceleration.3mf(7)
JerkAcceleration.3mf(8)
JerkAcceleration.3mf(9)
JerkAcceleration.3mf(10)
JerkAcceleration.3mf(11)
JerkAcceleration.3mf(12)
JerkAcceleration.3mf(13)
JerkAcceleration.3mf(14)
JerkAcceleration.3mf(15)

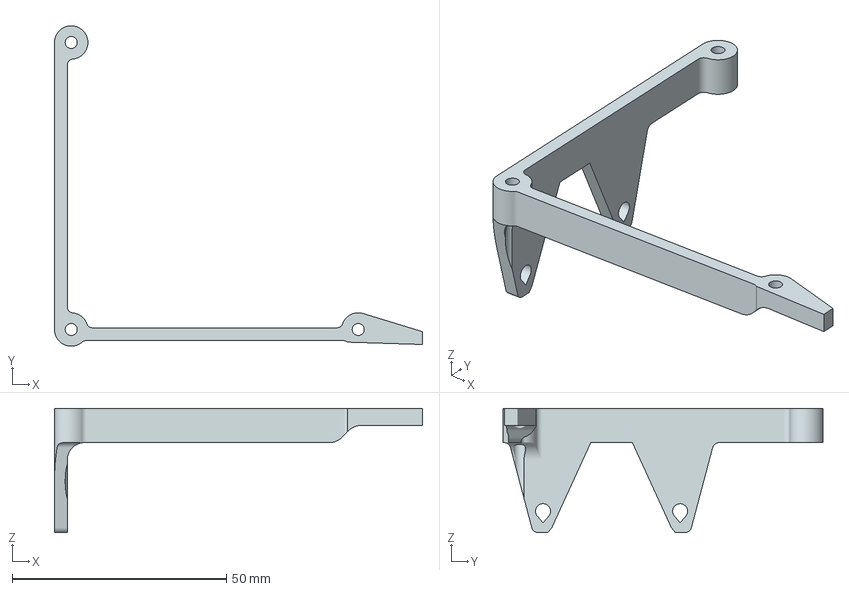
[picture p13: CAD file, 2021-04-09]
DoogellVega/CustomUpgrades/FanMount.3mf
85.9 x 74.8 x 29.0 mm

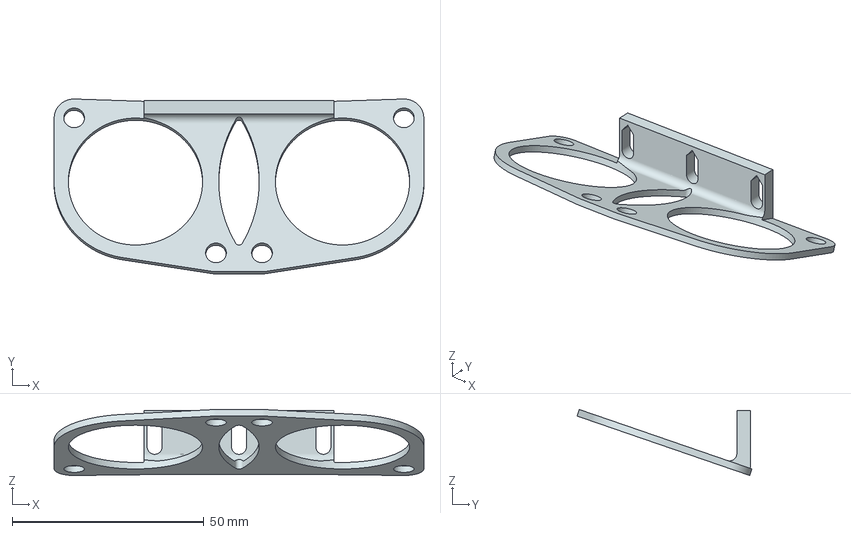
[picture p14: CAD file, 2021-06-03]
Raise3D_Pro2/CustomUpgrades/BlowerFanMount/BlowerFanMountFront.3mf
96.5 x 45.6 x 17.2 mm

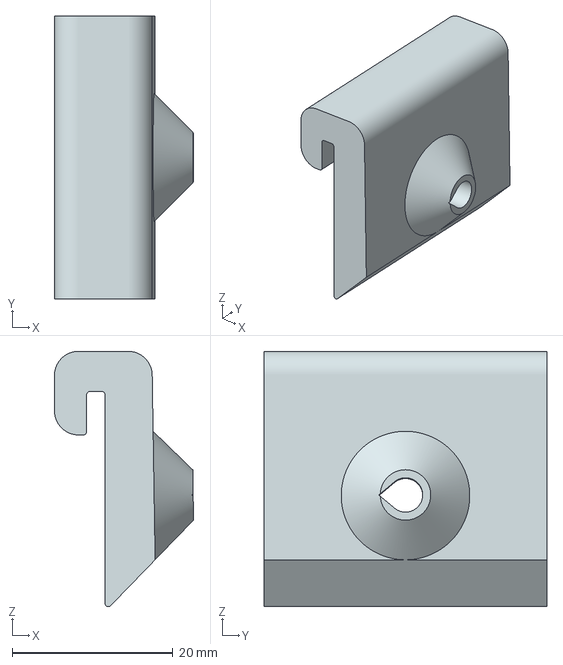
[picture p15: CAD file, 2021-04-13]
Raise3D_Pro2/CustomUpgrades/FilamentSpoolMount/FilamentSpoolMount-Hook.3mf
17.3 x 35.2 x 31.8 mm

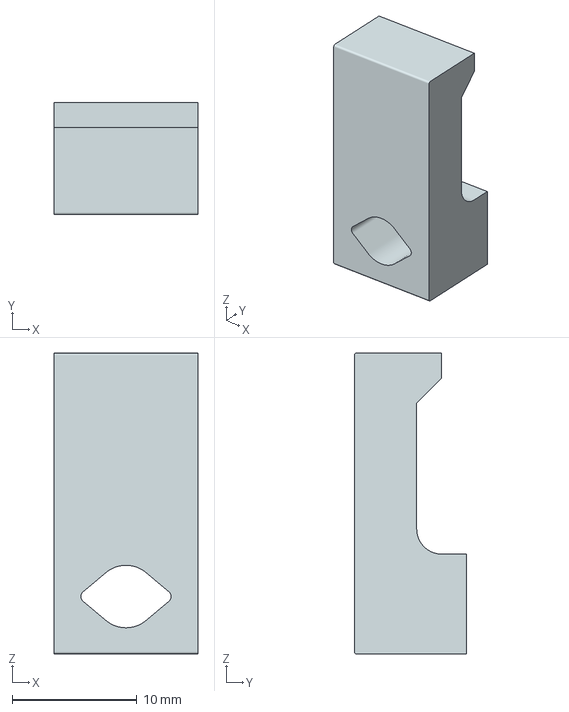
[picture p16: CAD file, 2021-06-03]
Raise3D_Pro2/CustomUpgrades/GlassBedMountsBack.3mf
11.5 x 9.00 x 24.1 mm

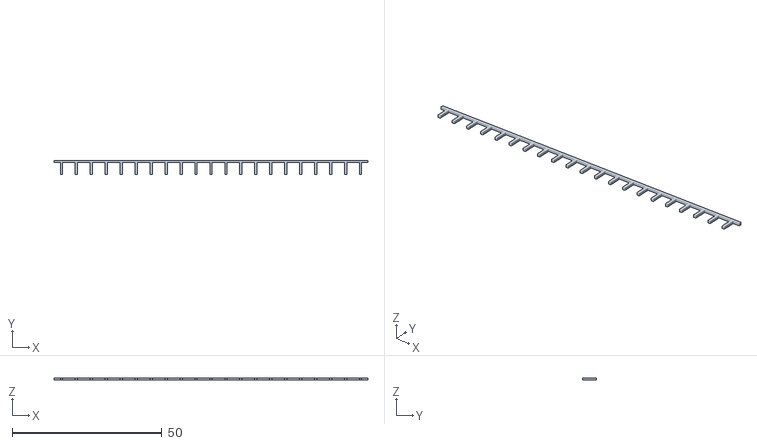
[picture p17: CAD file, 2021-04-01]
CalibrationObjects/DualExtruderCalibration/dual_calibration_v2_a.stl
105.0 x 4.80 x 0.8

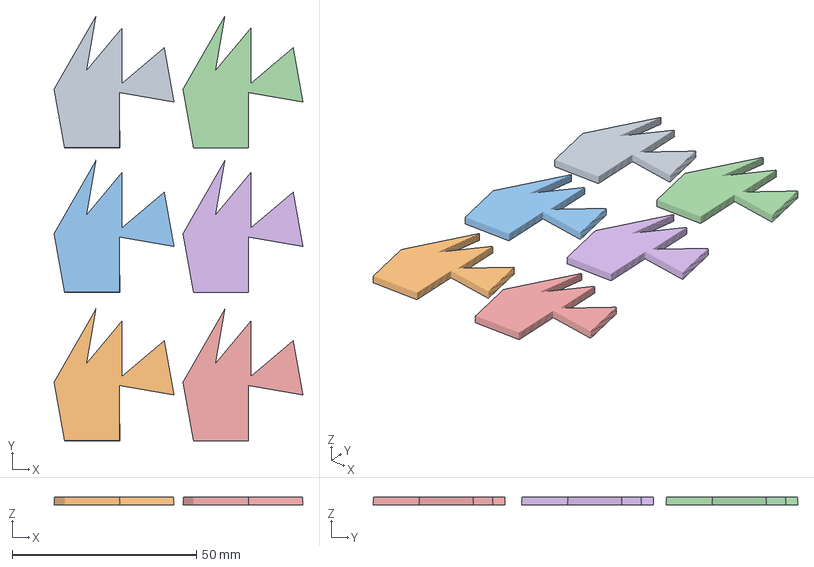
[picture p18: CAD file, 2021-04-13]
CalibrationObjects/JerkOnly.3mf
67.6 x 115.4 x 2.10 mm
JerkOnly.3mf
JerkOnly.3mf(1)
JerkOnly.3mf(2)
JerkOnly.3mf(3)
JerkOnly.3mf(4)
JerkOnly.3mf(5)

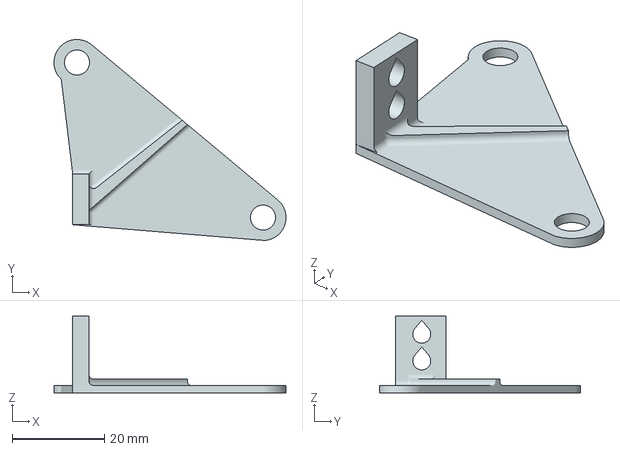
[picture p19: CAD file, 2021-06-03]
Raise3D_Pro2/CustomUpgrades/BlowerFanMount/BlowerFanMountRight.3mf
50.3 x 43.6 x 16.6 mm

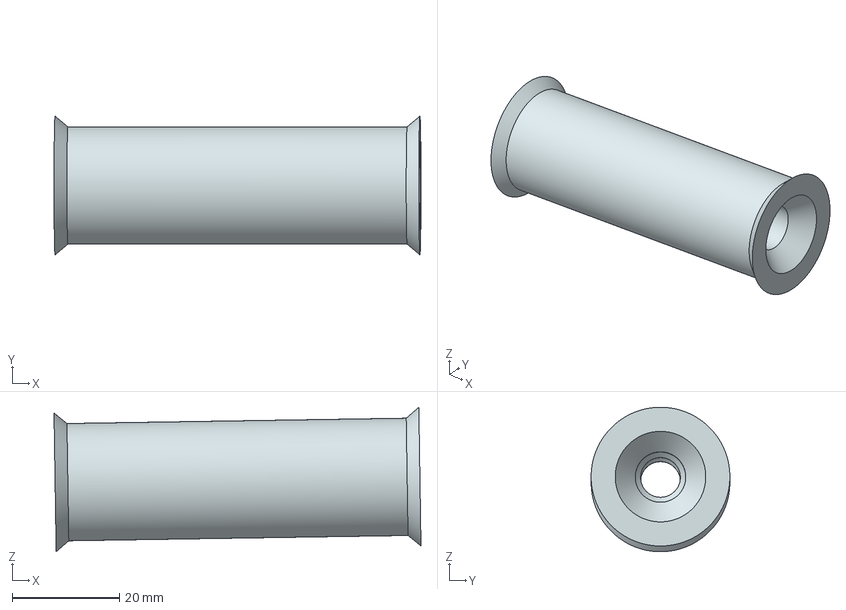
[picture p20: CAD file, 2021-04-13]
Raise3D_Pro2/CustomUpgrades/FilamentSpoolMount/FilamentSpoolMount-BearingHousing.3mf
68.4 x 25.9 x 26.9 mm

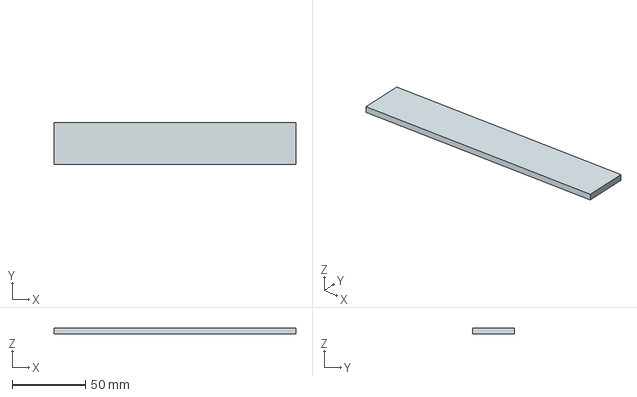
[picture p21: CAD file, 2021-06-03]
Raise3D_Pro2/CustomUpgrades/GlassBedMountsFrontLong.3mf
165.2 x 29.0 x 3.80 mm

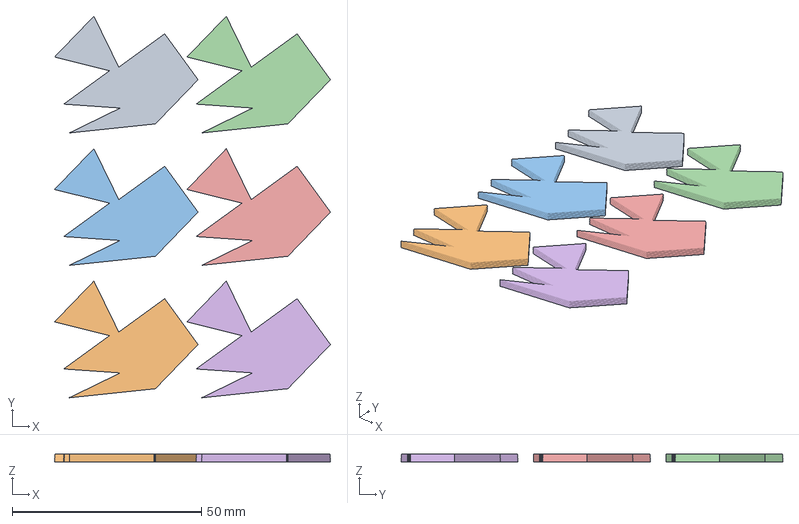
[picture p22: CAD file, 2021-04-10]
CalibrationObjects/AccelerationOnly.3mf
73.0 x 100.9 x 2.10 mm
JerkAccelerationTest.3mf
JerkAccelerationTest.3mf(2)
JerkAccelerationTest.3mf(3)
JerkAccelerationTest.3mf(7)
JerkAccelerationTest.3mf(5)
JerkAccelerationTest.3mf(4)

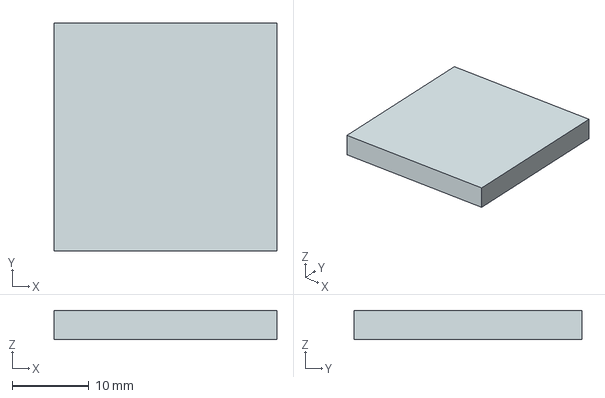
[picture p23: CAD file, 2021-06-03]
Raise3D_Pro2/CustomUpgrades/GlassBedMountsFrontShort.3mf
29.0 x 29.6 x 3.80 mm

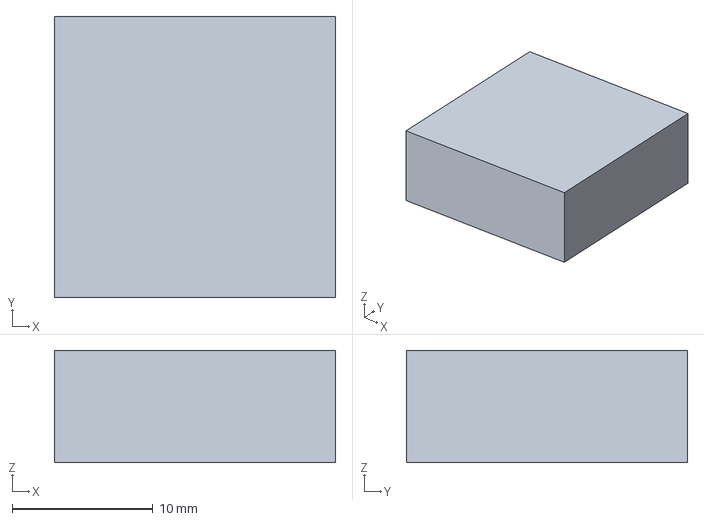
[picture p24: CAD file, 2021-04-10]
CalibrationObjects/FlowRateBox.3mf
20.0 x 20.0 x 8.00 mm

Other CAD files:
CalibrationObjects/FlowRateCylinder.3mf
CalibrationObjects/OverhangAngleTest.3mf
CalibrationObjects/StringingTest.3mf
CalibrationObjects/HorizontalExpansion&ToleranceTest.3mf
CalibrationObjects/FlowRateCylinder.prt
CalibrationObjects/HorizontalExpansion&ToleranceTest.prt
CalibrationObjects/JerkAccelerationSpeed.prt
CalibrationObjects/TemperatureTower.3mf
DoogellVega/CustomUpgrades/FanMount.prt
DoogellVega/CustomUpgrades/FilamentMount/ASM_Main.prt
DoogellVega/CustomUpgrades/FilamentMount/DoogellVegaTopPlate.prt
DoogellVega/CustomUpgrades/FilamentMount/FilamentMount.prt
DoogellVega/CustomUpgrades/GlassBed/2020BeamX.prt
DoogellVega/CustomUpgrades/GlassBed/2020BeamY.prt
DoogellVega/CustomUpgrades/GlassBed/2020BeamZ.prt
DoogellVega/CustomUpgrades/GlassBed/ASM_Bearing.prt
DoogellVega/CustomUpgrades/GlassBed/ASM_DoogellVegaBedSupport.prt
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

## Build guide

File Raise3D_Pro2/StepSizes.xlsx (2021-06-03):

 | X/Y Resolution |  | Z Resolution
1 | 0.0078125 | 0.0078125 | 0.00078125 | 0.000781 | X/Y | 0.125
2 |  | 0.0156250 |  | 0.001563 | Z | 0.025
3 |  | 0.0234375 |  | 0.002344
4 |  | 0.0312500 |  | 0.003125
5 |  | 0.0390625 |  | 0.003906
6 |  | 0.0468750 |  | 0.004688
7 |  | 0.0546875 |  | 0.005469
8 |  | 0.0625000 |  | 0.006250
9 |  | 0.0703125 |  | 0.007031
10 |  | 0.0781250 |  | 0.007812
11 |  | 0.0859375 |  | 0.008594
12 |  | 0.0937500 |  | 0.009375
13 |  | 0.1015625 |  | 0.010156
14 |  | 0.1093750 |  | 0.010938
15 |  | 0.1171875 |  | 0.011719
16 |  | 0.1250000 |  | 0.012500
17 |  | 0.1328125 |  | 0.013281
18 |  | 0.1406250 |  | 0.014063
19 |  | 0.1484375 |  | 0.014844
20 |  | 0.1562500 |  | 0.015625
21 |  | 0.1640625 |  | 0.016406
22 |  | 0.1718750 |  | 0.017188
23 |  | 0.1796875 |  | 0.017969
24 |  | 0.1875000 |  | 0.018750
25 |  | 0.1953125 |  | 0.019531
26 |  | 0.2031250 |  | 0.020313
27 |  | 0.2109375 |  | 0.021094
28 |  | 0.2187500 |  | 0.021875
29 |  | 0.2265625 |  | 0.022656
30 |  | 0.2343750 |  | 0.023438
31 |  | 0.2421875 |  | 0.024219
32 |  | 0.2500000 |  | 0.025000
33 |  | 0.2578125 |  | 0.025781
34 |  | 0.2656250 |  | 0.026563
35 |  | 0.2734375 |  | 0.027344
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

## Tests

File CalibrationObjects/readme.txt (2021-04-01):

Stack the [Smart compact temperature calibration Towers](https://www.thingiverse.com/thing:2729076) on top of each other in Cura. Make sure you import the models only (without importing profiles)! Once imported, use "Extensions" -> "Post Processing" -> "ChangeAtZ" to set the temperatures at different heights (1.4mm, 11.4mm, 21.4mm ...).  
Infill = 15%;  
Support = No;  
Build Plate Adhesion = Skirt;

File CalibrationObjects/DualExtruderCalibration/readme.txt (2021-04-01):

https://www.thingiverse.com/thing:2362201

First eyeball the offsets so the extruders fall in around 1mm range when switching between them (use T0 and T1 command).

Load both objects into your slicer without any offset. Assign each to a different extruder and print. They should be able to bind together without any overlap if your extruder offset is close enough.

After printing the object, find the short line that align best with the line on its opposite side, count how many short lines are on its left and right. If it's 10 vs 10, that means a perfect alignment. If not, change the offset value by 0.1 * (numOfShortLineOnLeft - 10), then print again to verify.

After finishing X axis, rotate the objects by 90 degrees to calibrate Y axis.

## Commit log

2020-06-10 add glass bed support
    [2020BeamX.prt, 2020BeamY.prt, 2020BeamZ.prt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]
2020-06-10 update project progress
    [2020BeamX.prt, 2020BeamY.prt, 2020BeamZ.prt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]
2021-02-26 reorgasize folders
    [2020BeamX.prt, 2020BeamY.prt, 2020BeamZ.prt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]
2021-03-19 add 1.31
    [ASM_Main.prt, FanMount.prt, TopCoverMount.prt]
2021-04-20 publish v 1.5
    [Body1.stl, Duct.stl, FlowRateCube.3mf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]
